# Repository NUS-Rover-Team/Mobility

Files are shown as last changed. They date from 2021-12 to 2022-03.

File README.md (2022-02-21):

# Mobility

The mobility system of the rover is comprised of a wheel sub-assembly, rocker-bogie suspension and a differential joint connecting the suspension to the chassis. 

## Rocker Bogie Suspension
This suspension was chosen to ensure the chassis remains parallel to the ground at all times. Furthermore, the system is designed such that the rover can traverse objects up to 30cm in height, without compromising the stability of the system. All components in the suspension are manufactured using Aluminium 6065, which was chosen for its light weight, tensile strength and manufacturability. 

## Wheels and Motors
The wheels on New Opportunity are made from durable, puncture-resistant rubber and are inflatable. This allows us to adjust the pressure within the wheels based on the terrain. 170KV brushless DC motors by Alien Power Systems were chosen since they provide high torque at a low RPM, have sufficient documentation and are reliable. The motors are controlled via Flipsky VESCs using PPM signals from the on-board ATmega328P-based microcontroller. 

## Suspension-Chassis Joint
The self-levelling mechanism is guided by the rotating differential bar attached to the chassis and rocker. 

## Control Scheme
The rover is steered using a 6-wheeled differential drive mechanism. The six wheels on the rover rotate at different velocities to achieve a desired rotation/movement. The control input comes from a joystick/autonomous command, which provides coordinates to the microcontroller, which in turn runs the motors at calculated velocities. The control scheme also uses a PID controller with a negative feedback loop to account for differences in velocities which may occur due to terrain/obstacles.

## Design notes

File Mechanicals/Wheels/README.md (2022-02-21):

# How to fix the wheels to the motor mounts and motors?

## Step 1: Grab one of the inflated wheels, place it like this:

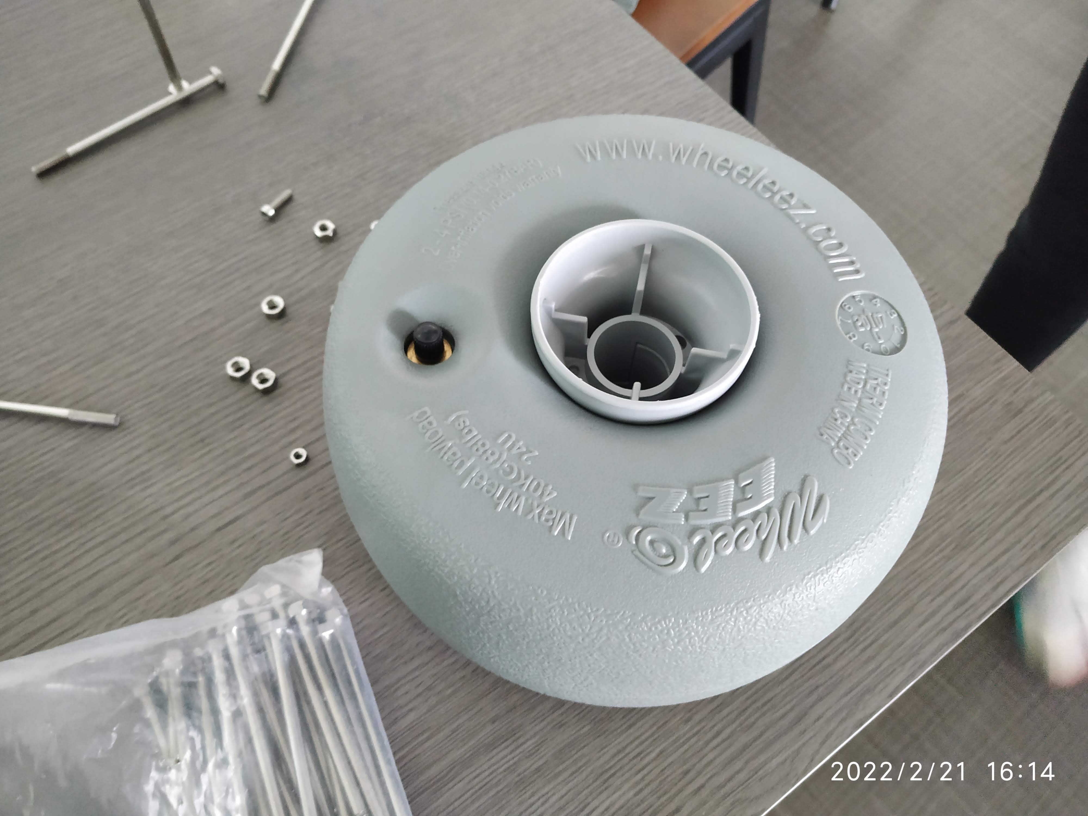
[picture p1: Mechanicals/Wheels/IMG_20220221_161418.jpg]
Step1


## Step 2: Add the plastic circular connector to the centre, make sure it aligns with the holes in the centre:

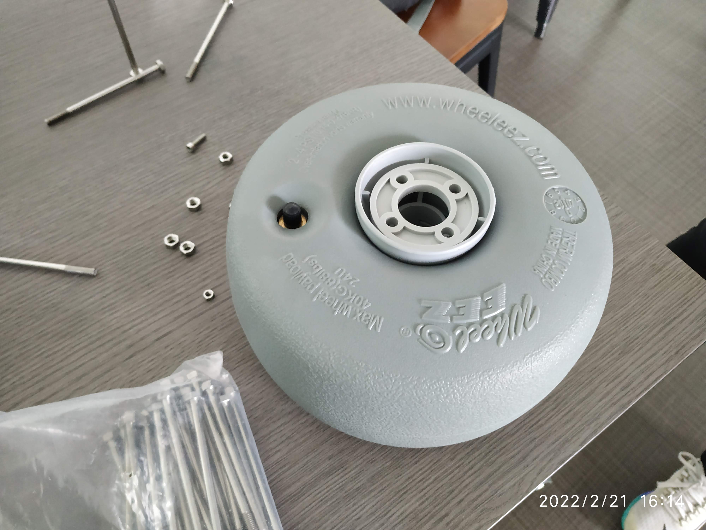
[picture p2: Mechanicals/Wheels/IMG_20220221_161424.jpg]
Step2


## Step 3: Flip it over and add the large screws in the 4 holes 

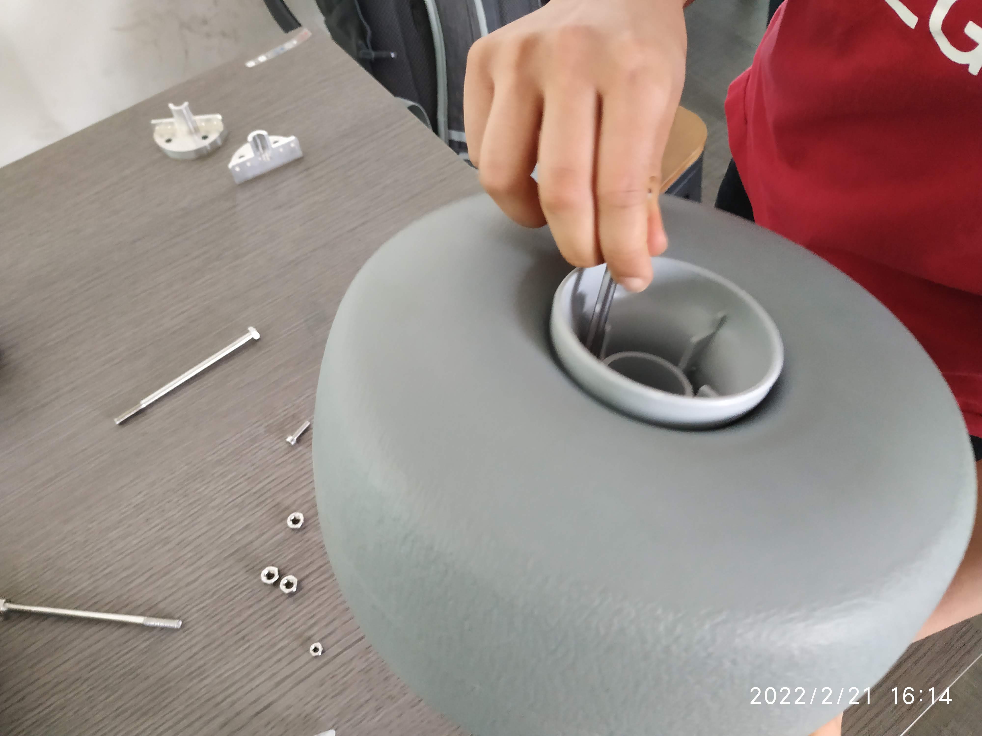
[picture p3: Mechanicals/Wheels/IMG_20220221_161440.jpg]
Step 3


## Step 4: It should look like this:

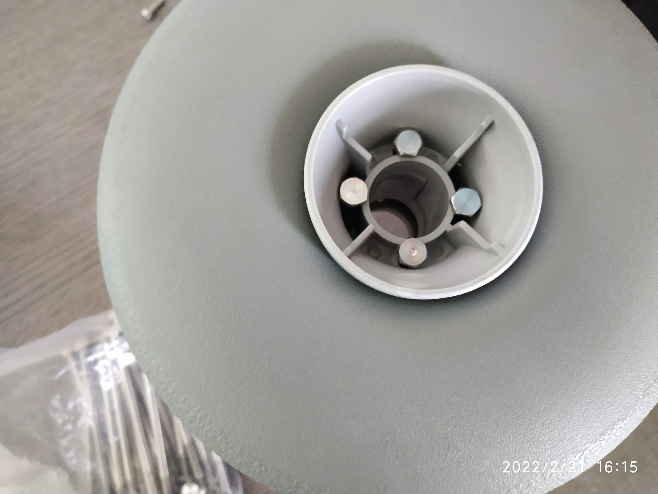
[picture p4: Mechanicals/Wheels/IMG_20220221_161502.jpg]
Step 4


## Step 5: Flip it over it will look something like this. You must hold on to the screws at this point or they'll fall out.

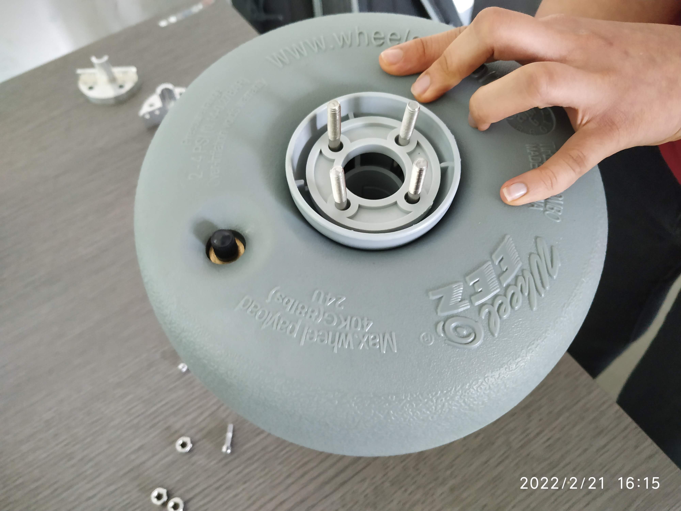
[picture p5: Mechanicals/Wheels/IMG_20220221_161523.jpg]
Step 5


## Step 6: Add the metal connector clamp to this. Most of them have a fixed pair they clamp well with in the lab. 

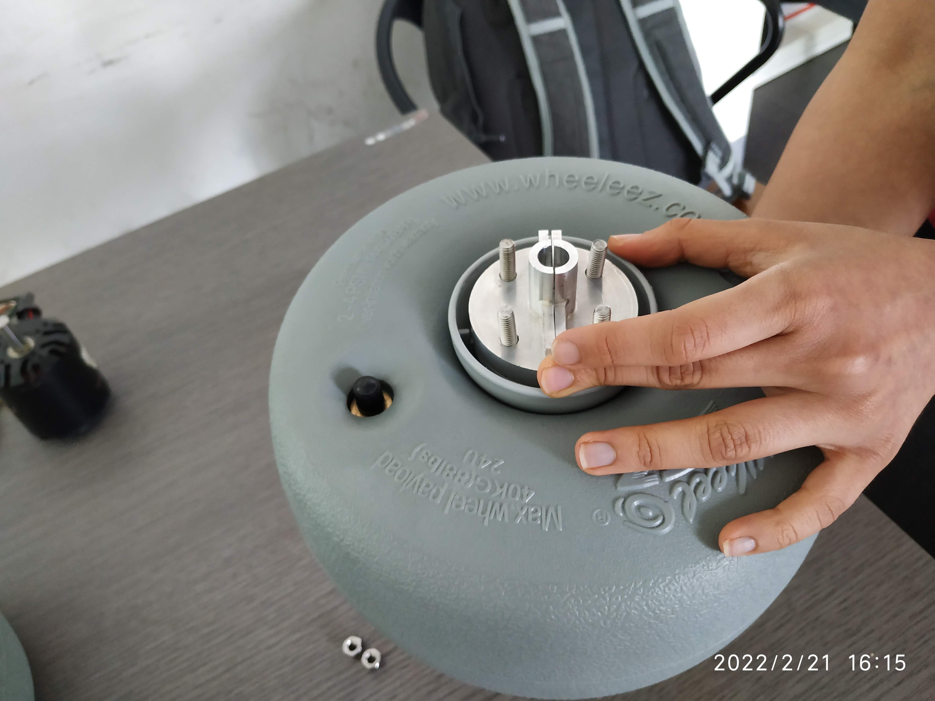
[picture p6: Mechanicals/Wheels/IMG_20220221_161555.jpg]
Step 6


## Step 7: Screw on the nuts for the large screws to hold everything in place:

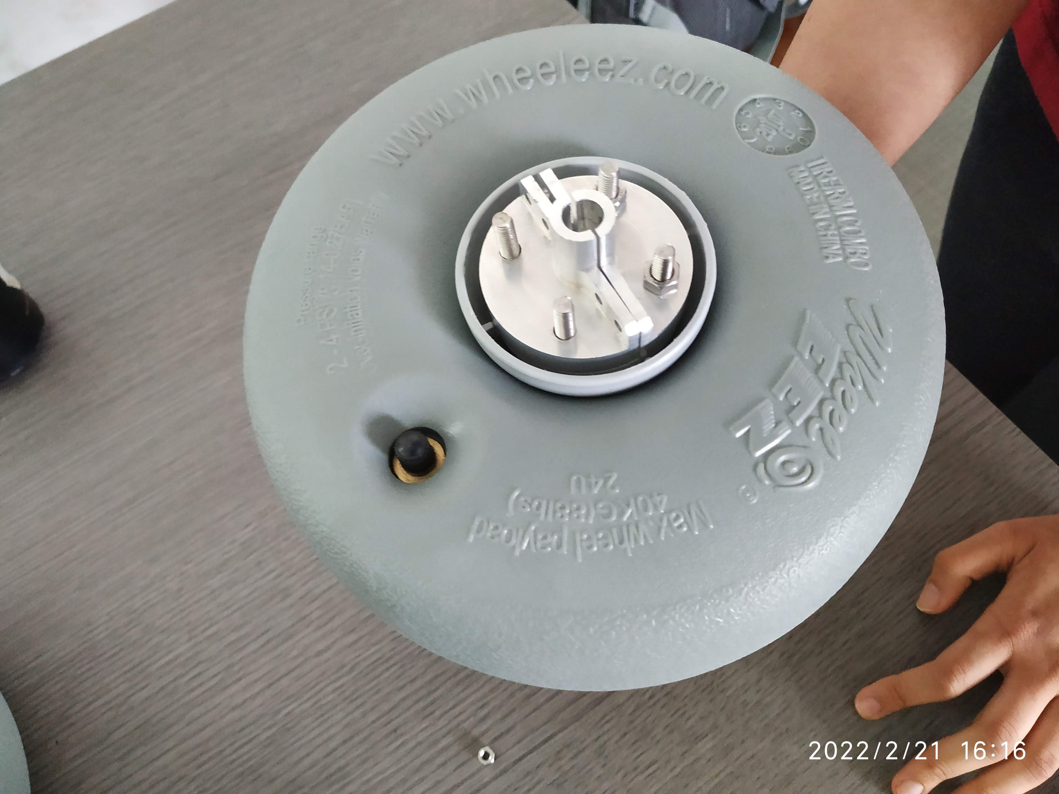
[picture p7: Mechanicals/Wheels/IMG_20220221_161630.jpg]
Step 7


## Step 8: Put the motor shaft in the connector

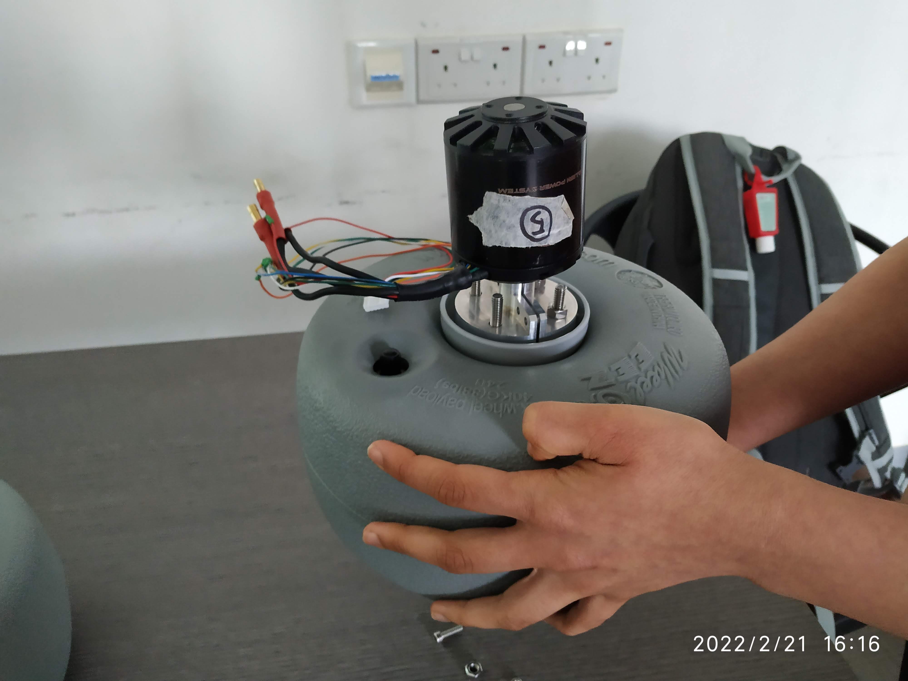
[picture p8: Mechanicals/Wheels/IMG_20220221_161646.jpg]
Step 8


## Step 9: Fasten the connector with M5 screws and nuts:

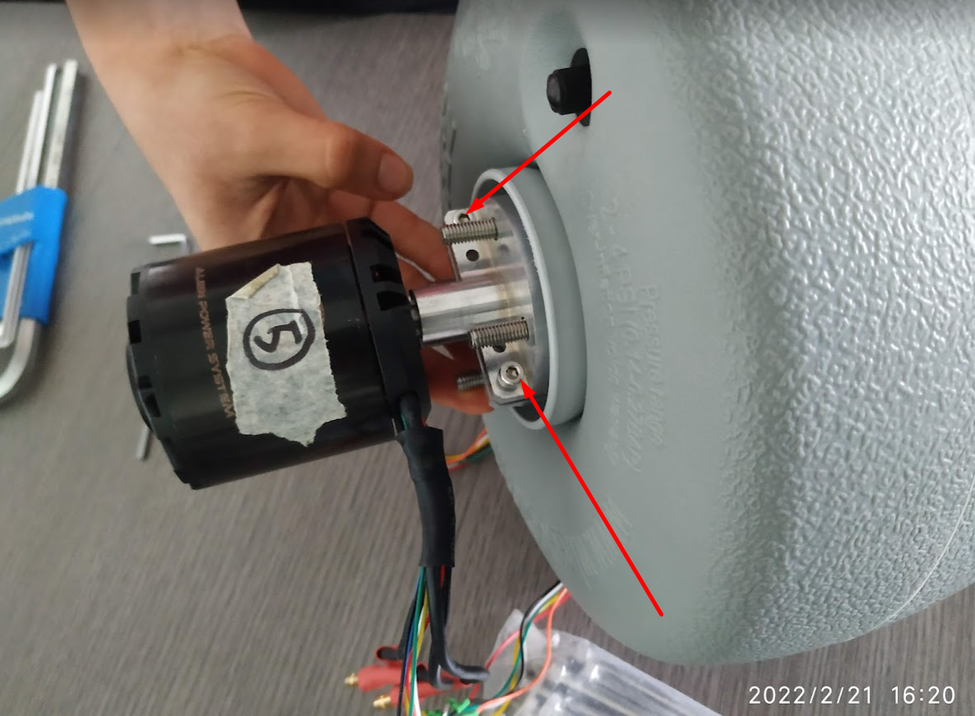
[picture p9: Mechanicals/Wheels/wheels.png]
Step 9


## Step 10: Slip the motor mount on and you're good to go!

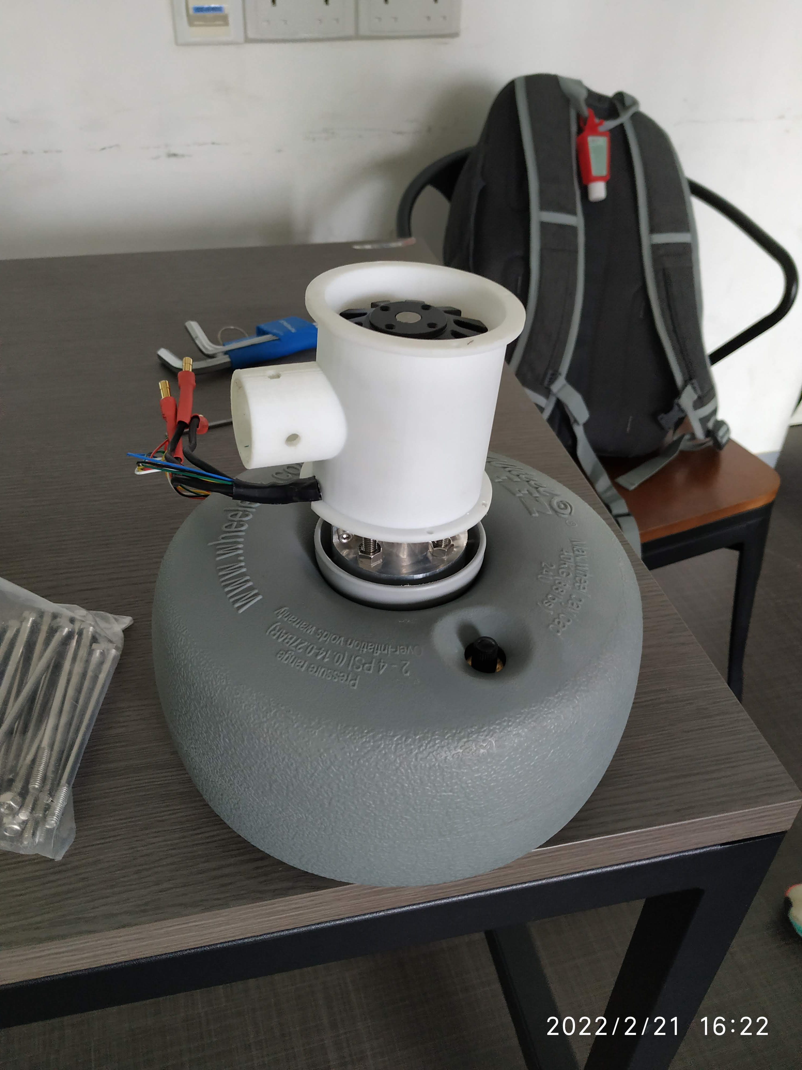
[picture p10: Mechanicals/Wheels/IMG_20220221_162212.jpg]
Step 10


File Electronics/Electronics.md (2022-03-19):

# Mobility Circuit

mobility-motor-circuit-diagram

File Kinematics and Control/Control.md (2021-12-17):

# Inv Kin for 6 Wheeled Differential Drive

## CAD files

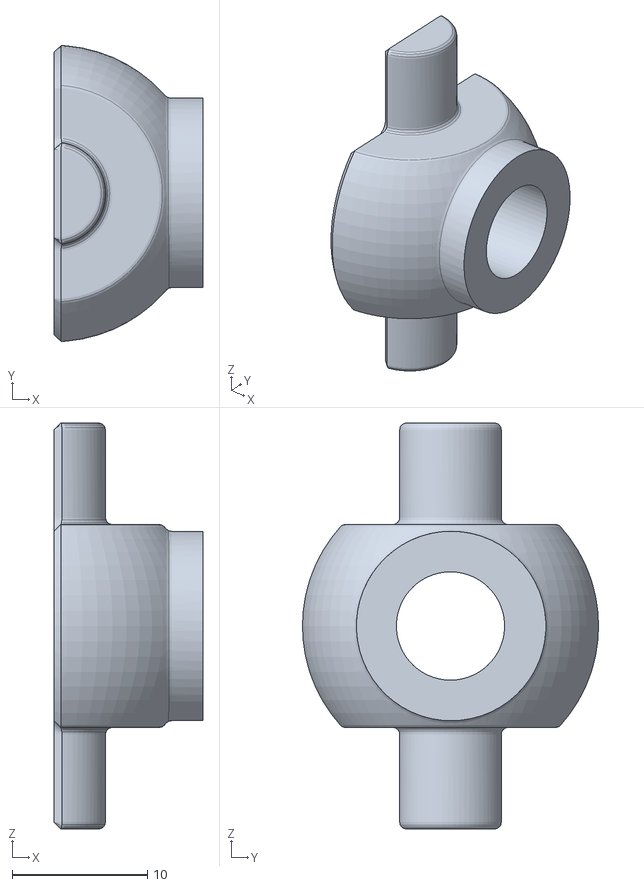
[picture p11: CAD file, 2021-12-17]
Mechanicals/New Differential Design (Sawppy)/Rod Support (QTY = 2).stl
11.0 x 21.9 x 30.0

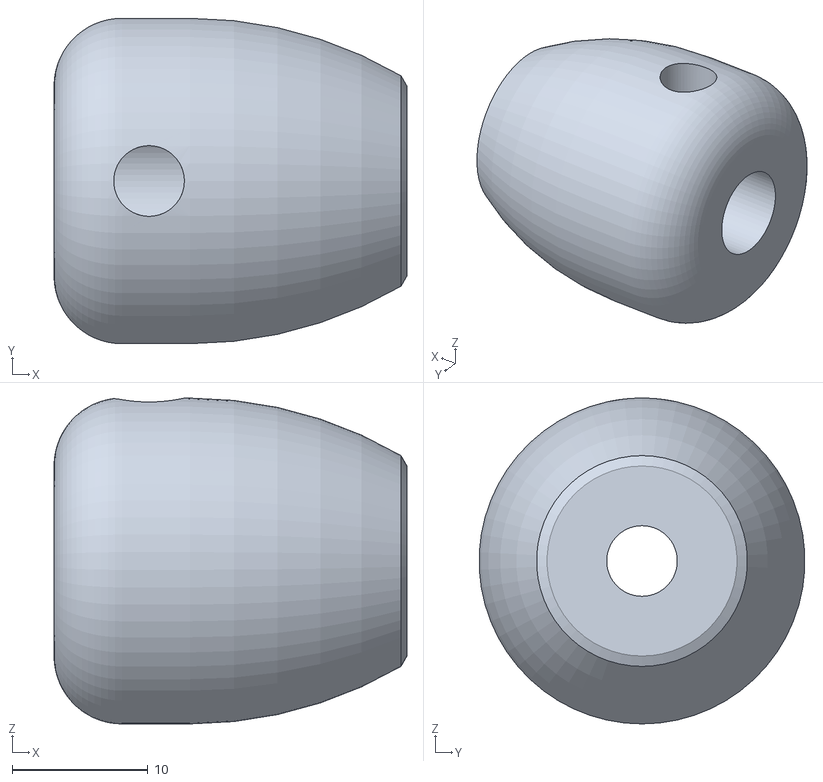
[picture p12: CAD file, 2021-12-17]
Mechanicals/New Differential Design (Sawppy)/DiffLink (QTY = 2).stl
26.0 x 24.0 x 24.0

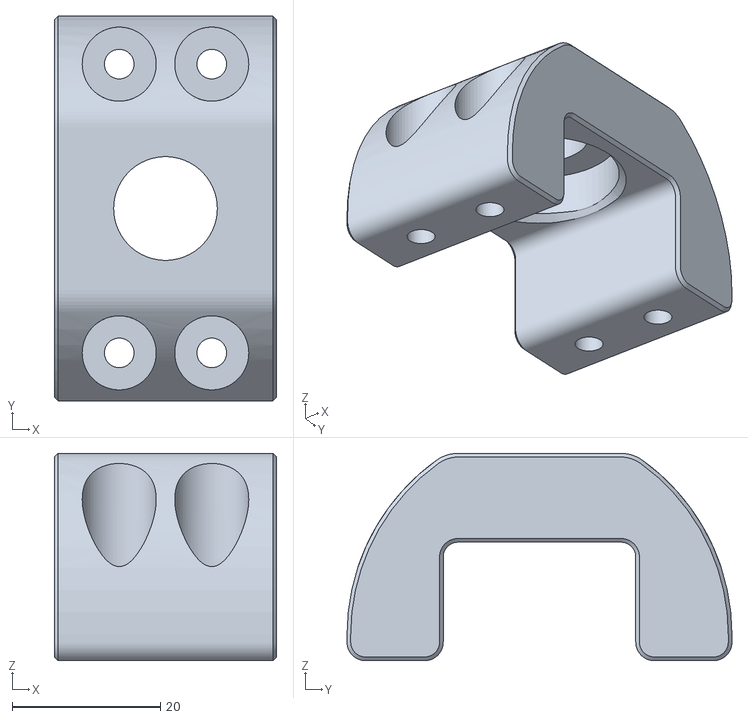
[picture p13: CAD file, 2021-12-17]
Mechanicals/New Differential Design (Sawppy)/DiffUpper (QTY = 1).stl
30.0 x 52.0 x 28.0

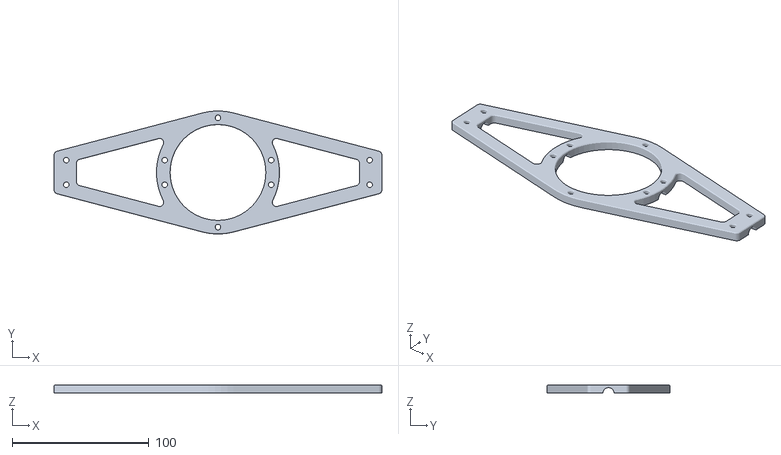
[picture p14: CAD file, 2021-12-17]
Mechanicals/New Differential Design (Sawppy)/DiffBrace (QTY = 2).stl
240.0 x 89.9 x 6.00

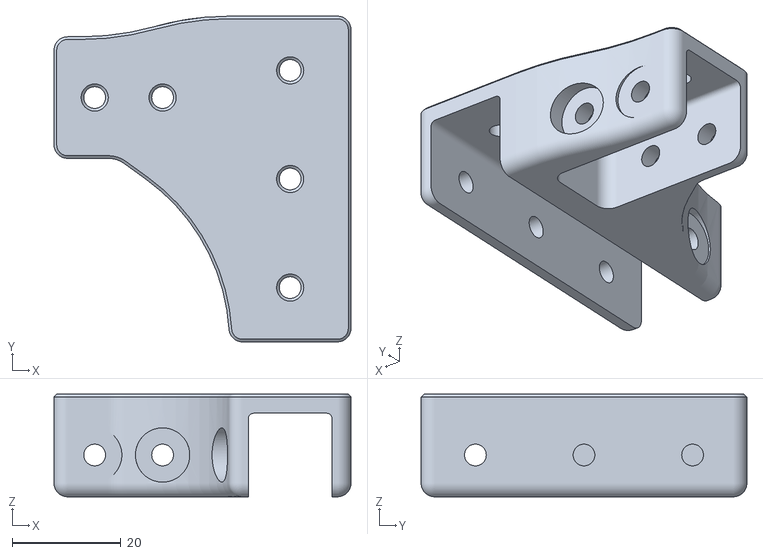
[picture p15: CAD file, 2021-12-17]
Mechanicals/New Differential Design (Sawppy)/DiffEnd (QTY = 2 MIRROR 1).stl
54.7 x 60.0 x 18.9

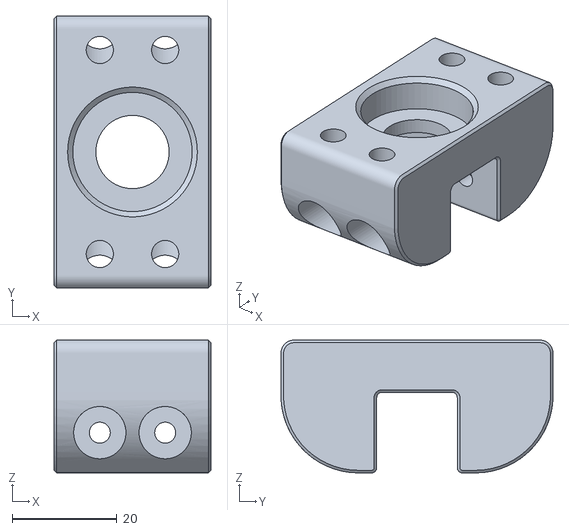
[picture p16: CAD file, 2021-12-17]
Mechanicals/New Differential Design (Sawppy)/DiffLower (QTY = 1).stl
30.0 x 52.0 x 25.4

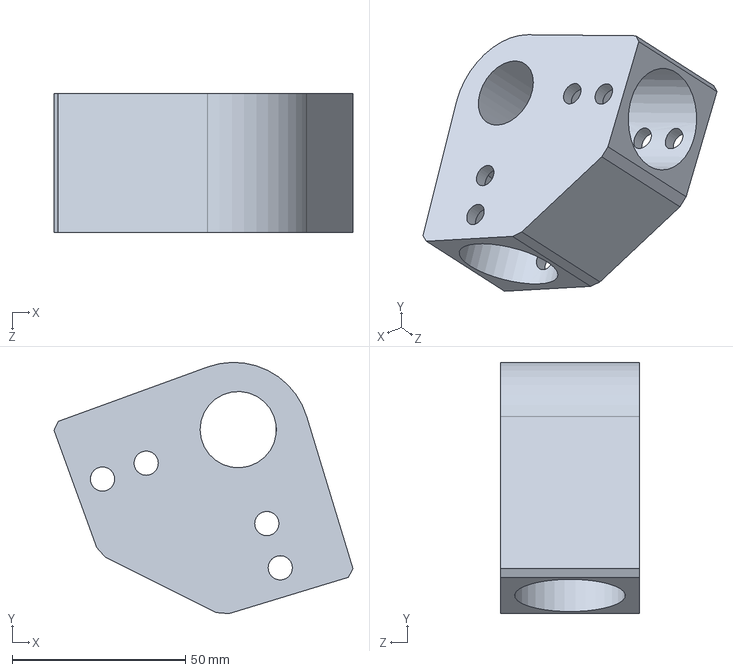
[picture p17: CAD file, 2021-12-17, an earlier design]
Mechanicals/Old Parts/Bogie/New Bogie Joint (QTY = 2).SLDPRT
86.2 x 72.5 x 40.0 mm

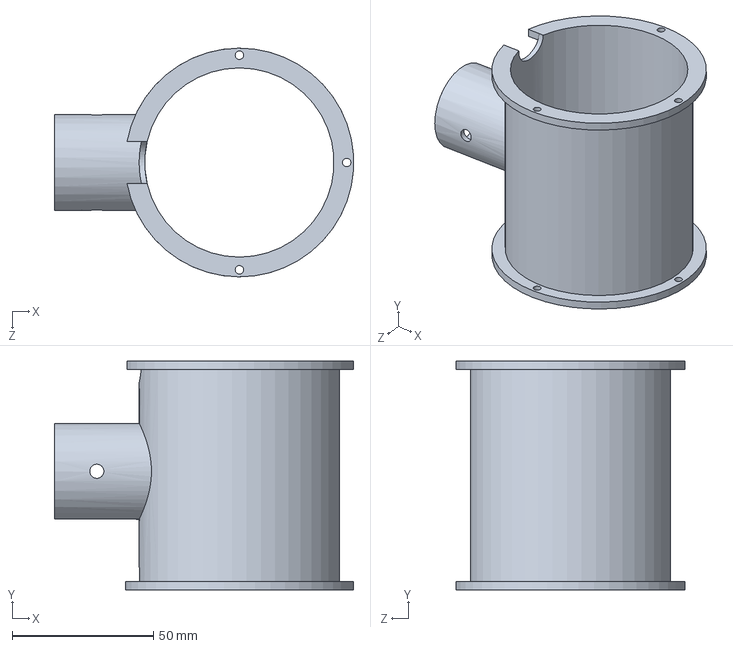
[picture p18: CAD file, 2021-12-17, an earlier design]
Mechanicals/Old Parts/Motor/Motor Housing New v1.1 (QTY = 6).SLDPRT
105.9 x 81.0 x 81.0 mm

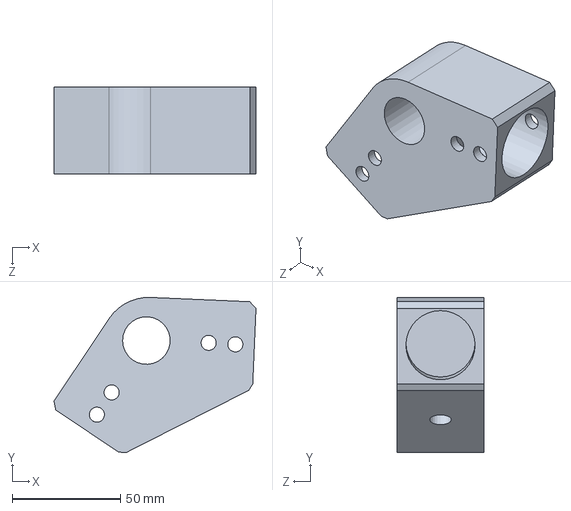
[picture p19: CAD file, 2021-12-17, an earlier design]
Mechanicals/Old Parts/Rocker/New Rocker Joint (QTY = 2).SLDPRT
93.4 x 71.7 x 40.0 mm

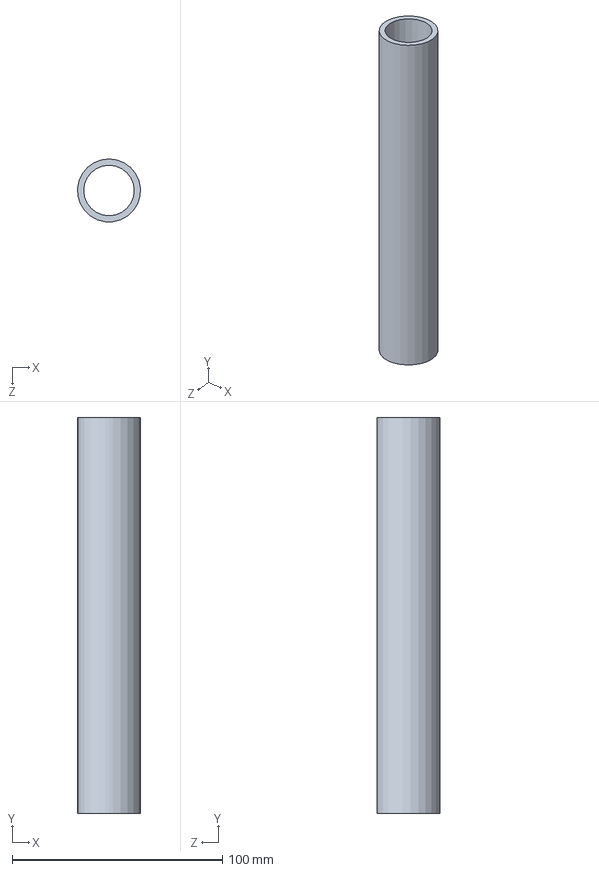
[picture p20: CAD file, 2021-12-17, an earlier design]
Mechanicals/Old Parts/Bogie/Bogie Rod (QTY = 4).SLDPRT
29.9 x 188.2 x 30.0 mm

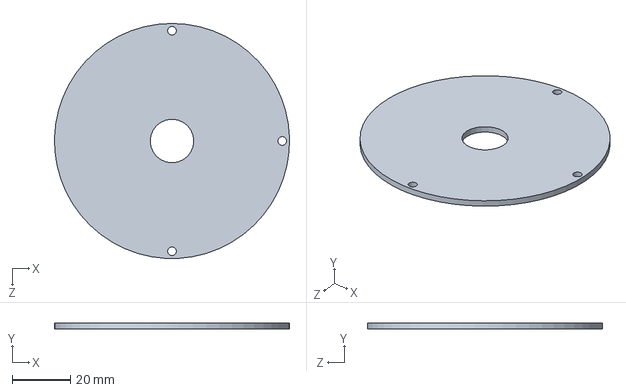
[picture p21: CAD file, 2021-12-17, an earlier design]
Mechanicals/Old Parts/Motor/Motor Housing Top Cover (QTY = 6).SLDPRT
81.0 x 2.00 x 81.0 mm

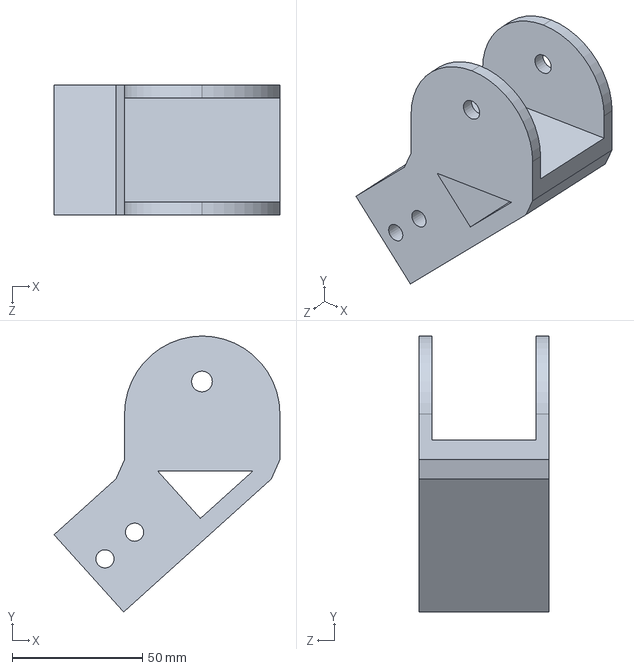
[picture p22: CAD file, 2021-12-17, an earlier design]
Mechanicals/Old Parts/Rocker/New Rocker Bracket (QTY = 2).SLDPRT
86.9 x 106.1 x 50.0 mm

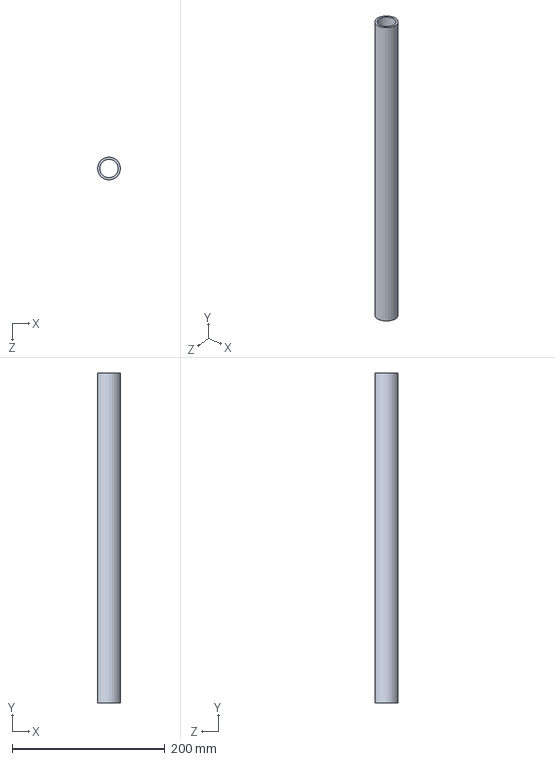
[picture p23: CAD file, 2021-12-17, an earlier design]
Mechanicals/Old Parts/Rocker/Rocker Rod Long (QTY = 2).SLDPRT
30.0 x 432.0 x 30.0 mm

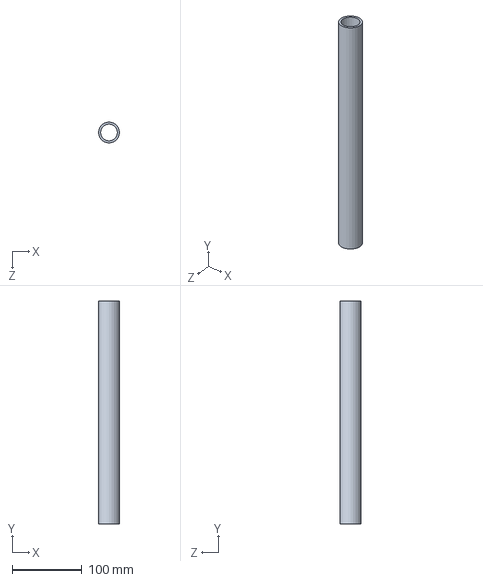
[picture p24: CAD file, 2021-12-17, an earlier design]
Mechanicals/Old Parts/Rocker/Rocker Rod short (QTY = 2).SLDPRT
30.0 x 320.0 x 30.0 mm

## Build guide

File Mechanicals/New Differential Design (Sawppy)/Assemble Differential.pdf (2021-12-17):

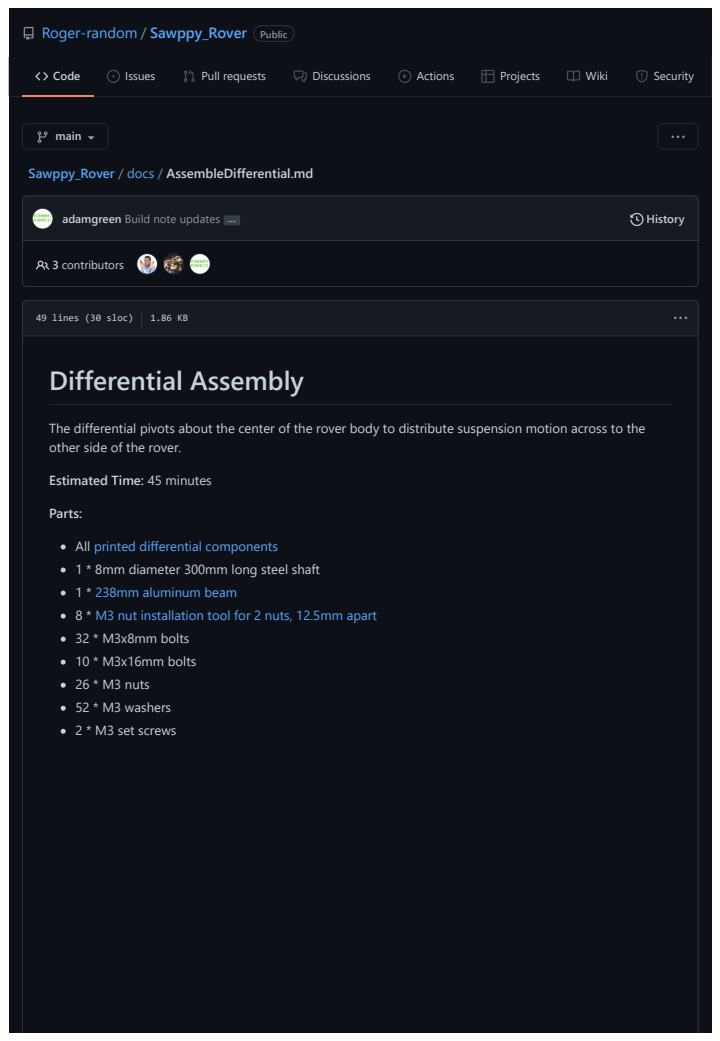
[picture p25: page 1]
Code; Issues; Pull requests; Discussions; Actions; Projects; Wiki; Security; adamgreen Build note updates …; History; 3 contributors; main; 49 lines (30 sloc); Differential Assembly

Roger-random (https://github.com/Roger-random) / Sawppy_Rover (https://github.com/Roger-random/Sawppy_Rover) Public

Sawppy_Rover (https://github.com/Roger-random/Sawppy_Rover) / docs (https://github.com/Roger-random/Sawppy_Rover/tree/main/docs) / AssembleDifferential.md

The differential pivots about the center of the rover body to distribute suspension motion across to the
other side of the rover.
Estimated Time: 45 minutes
Parts:
All printed differential components (https://github.com/Roger-random/Sawppy_Rover/blob/main/docs/Print%20Differential.md)
1 * 8mm diameter 300mm long steel shaft
1 * 238mm aluminum beam (https://github.com/Roger-random/Sawppy_Rover/blob/main/docs/Misumi%20HFS%203.md)
8 * M3 nut installation tool for 2 nuts, 12.5mm apart (https://github.com/Roger-random/Sawppy_Rover/blob/main/docs/Print%20M3%20Installation%20Tool.md)
32 * M3x8mm bolts
10 * M3x16mm bolts
26 * M3 nuts
52 * M3 washers
2 * M3 set screws

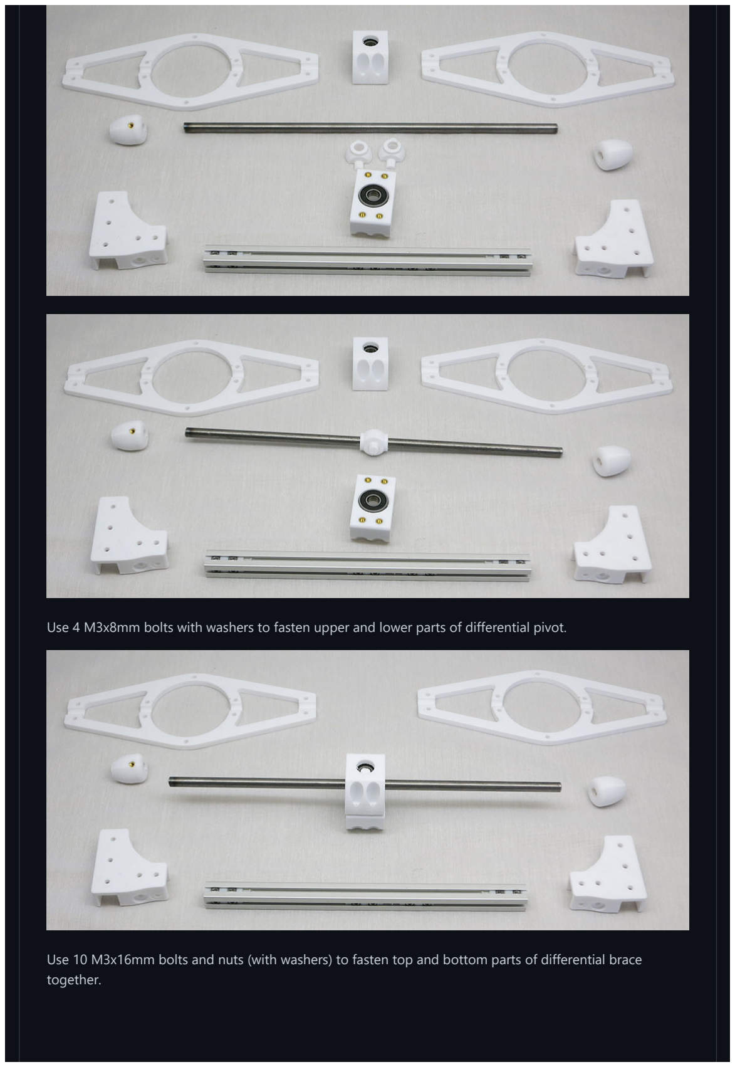
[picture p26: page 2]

Use 4 M3x8mm bolts with washers to fasten upper and lower parts of differential pivot.

Use 10 M3x16mm bolts and nuts (with washers) to fasten top and bottom parts of differential brace together.

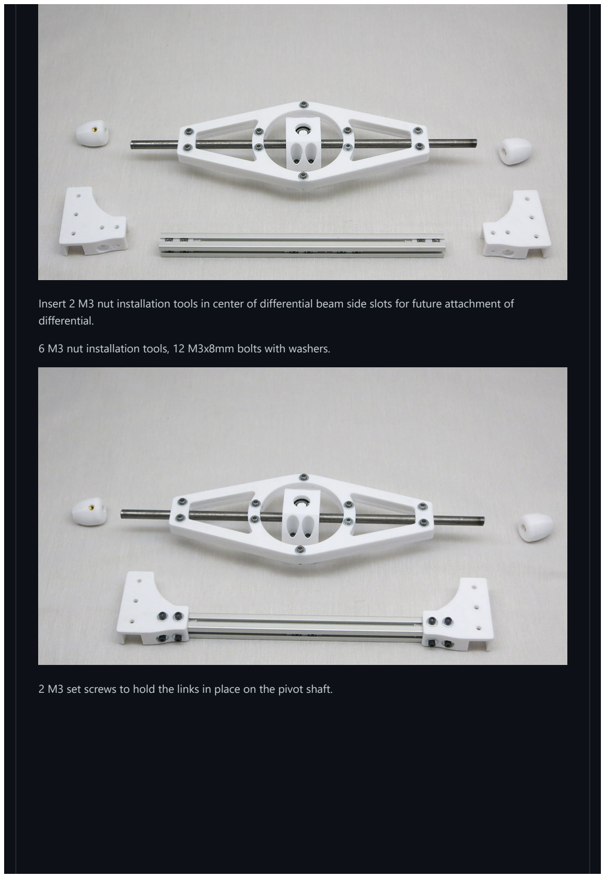
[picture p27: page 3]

Insert 2 M3 nut installation tools in center of differential beam side slots for future attachment of differential.

6 M3 nut installation tools, 12 M3x8mm bolts with washers.

2 M3 set screws to hold the links in place on the pivot shaft.

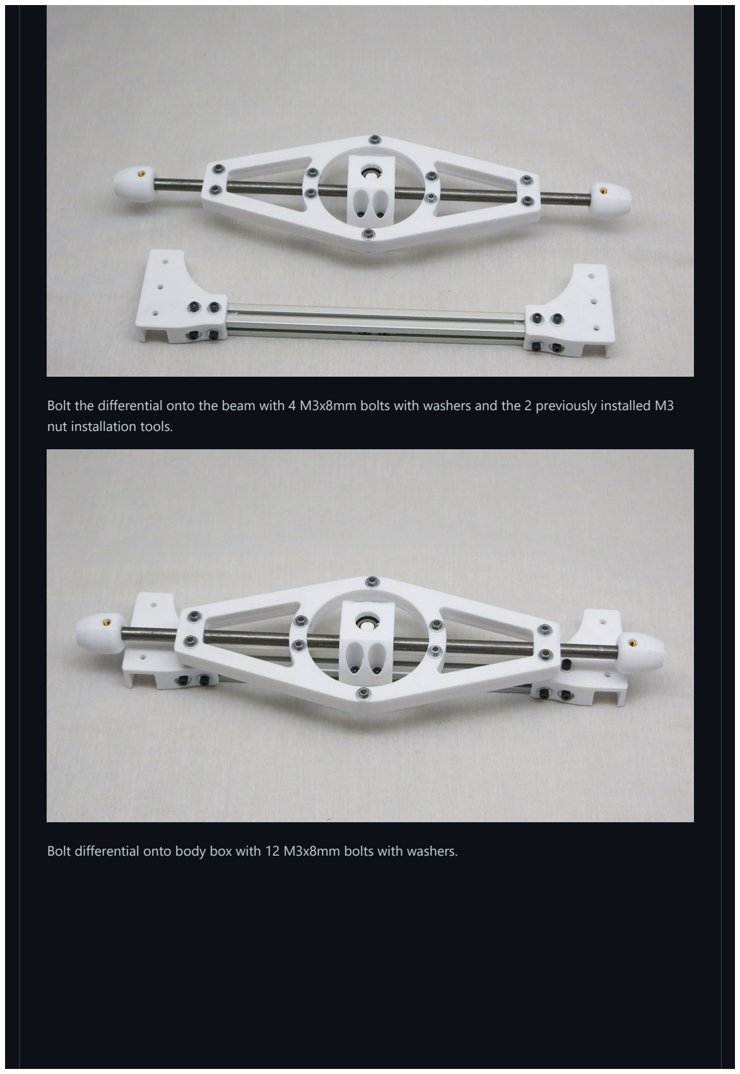
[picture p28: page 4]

Bolt the differential onto the beam with 4 M3x8mm bolts with washers and the 2 previously installed M3 nut installation tools.

Bolt differential onto body box with 12 M3x8mm bolts with washers.

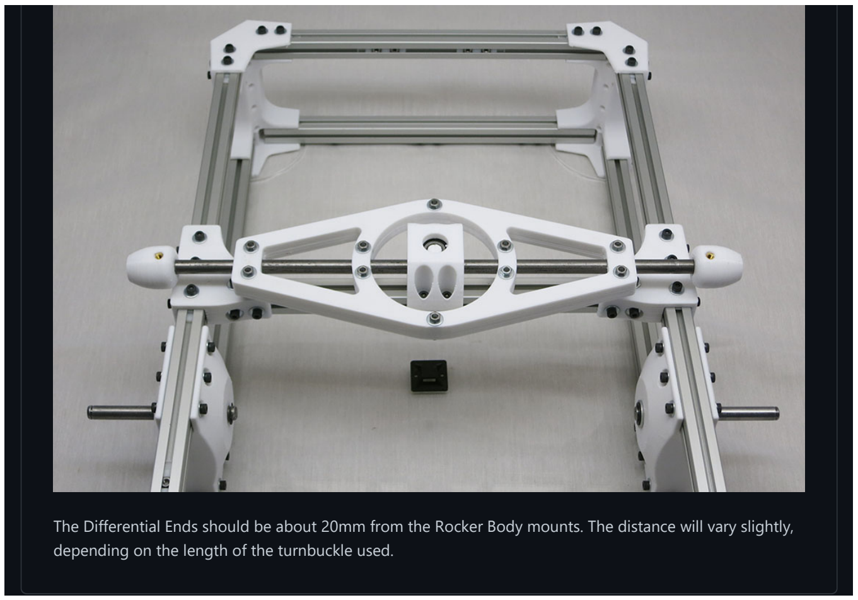
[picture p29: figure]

The Differential Ends should be about 20mm from the Rocker Body mounts. The distance will vary slightly, depending on the length of the turnbuckle used.

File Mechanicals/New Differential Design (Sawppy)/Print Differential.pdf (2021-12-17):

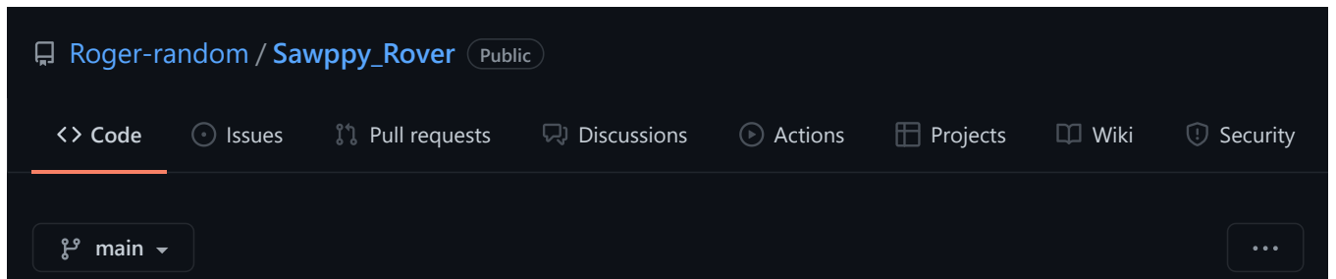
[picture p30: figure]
Roger-random / Sawppy_Rover Public; Code; Issues; Pull requests; Discussions; Actions; Projects; Wiki; Security; main

Sawppy_Rover (https://github.com/Roger-random/Sawppy_Rover) / docs (https://github.com/Roger-random/Sawppy_Rover/tree/main/docs) / Print Differential.md

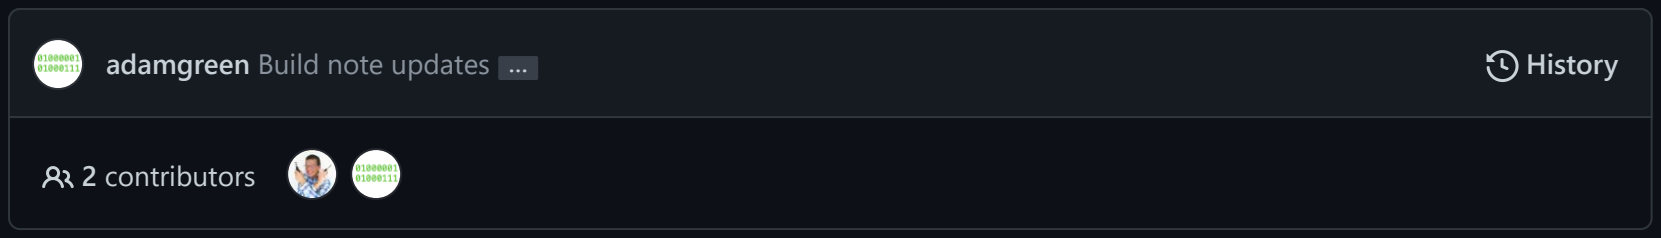
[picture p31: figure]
adamgreen Build note updates …; History; 2 contributors

43 lines (29 sloc) 2.07 KB

# Differential

The differential on Sawppy is different from the differential in an automotive drivetrain. Instead of distributing different forces across different drive wheels, this differential distributes suspension forces across the two sides. It is a key part of how the rocker-bogie suspension (https://en.wikipedia.org/wiki/Rocker-bogie) keeps all six wheels on the ground.

CAD source Differential (https://cad.onshape.com/documents/43678ef564a43281c83e1aef/w/392bbf8745395bc24367a35c/e/ded3b96eec03ac1553f6b0a8) with brackets to mount to body in Body Box Mounts (https://cad.onshape.com/documents/43678ef564a43281c83e1aef/w/392bbf8745395bc24367a35c/e/4b42dffa042b70b94b3d0d85)

3D Printing STL Files:

DiffBrace.stl (https://github.com/Roger-random/Sawppy_Rover/blob/main/STL/DiffBrace.stl) * 2
DiffEnd.stl (https://github.com/Roger-random/Sawppy_Rover/blob/main/STL/DiffEnd.stl) * 2 (Mirror one of them) DiffLink.stl (https://github.com/Roger-random/Sawppy_Rover/blob/main/STL/DiffLink.stl) * 2
DiffLower.stl (https://github.com/Roger-random/Sawppy_Rover/blob/main/STL/DiffLower.stl) * 1
DiffUpper.stl (https://github.com/Roger-random/Sawppy_Rover/blob/main/STL/DiffUpper.stl) * 1
Rod Support.stl (https://github.com/Roger-random/Sawppy_Rover/blob/main/STL/Rod%20Support.stl) * 2

3D Printing Notes:

The differential brace (https://github.com/Roger-random/Sawppy_Rover/blob/main/STL/DiffBrace.stl) is a large part that needs to be rotated 45 degrees in order to fit on a 200mm x 200mm print bed.
Aside from the differential brace, everything else can be printed together.

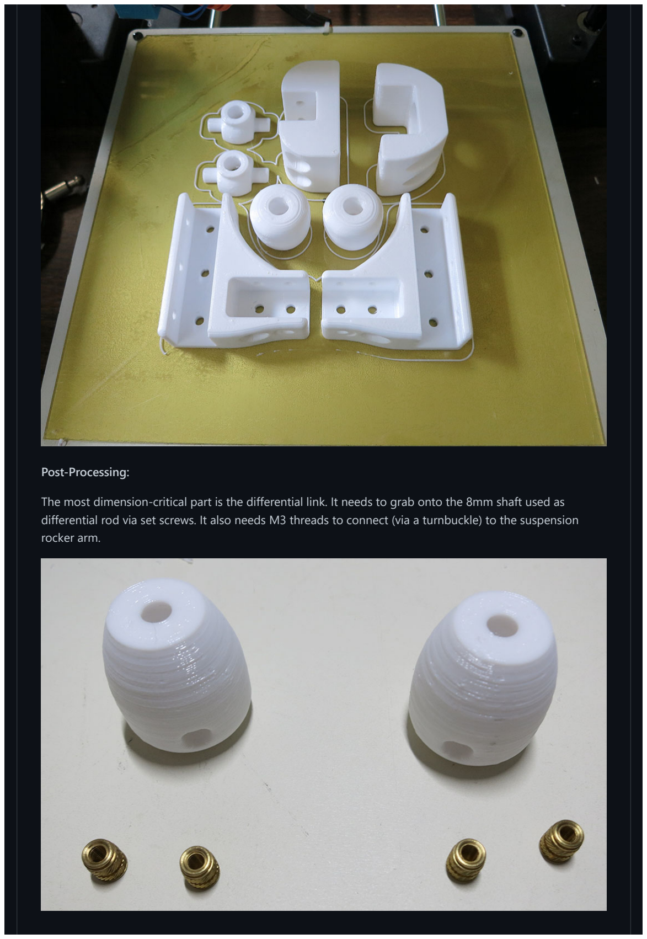
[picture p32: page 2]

Post-Processing:

The most dimension-critical part is the differential link. It needs to grab onto the 8mm shaft used as differential rod via set screws. It also needs M3 threads to connect (via a turnbuckle) to the suspension rocker arm.

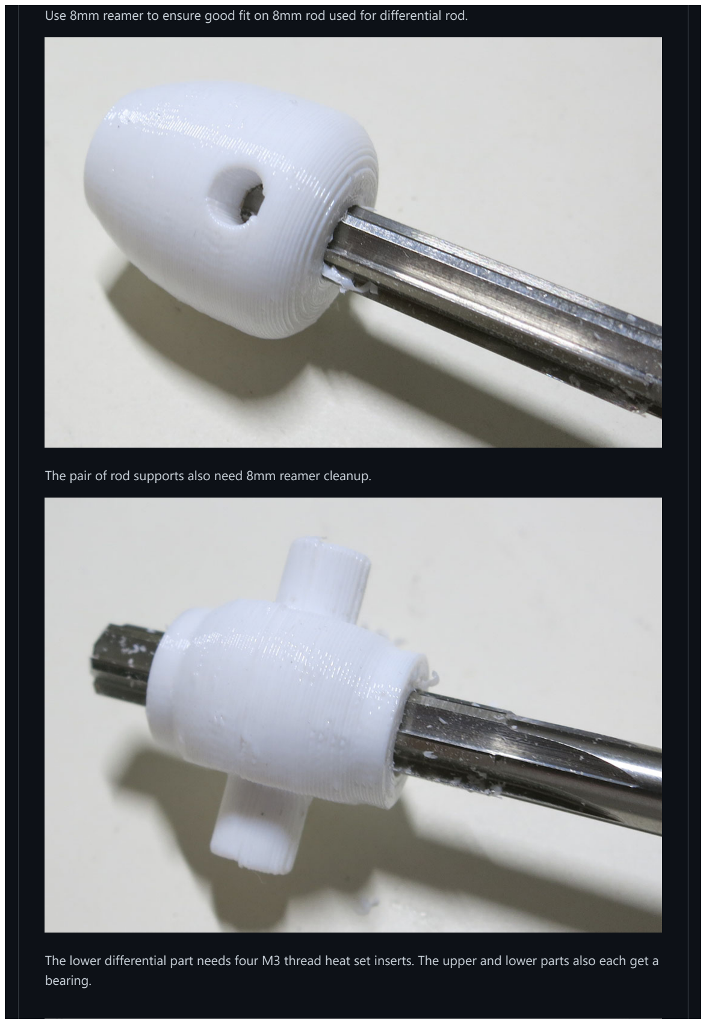
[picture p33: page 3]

Use 8mm reamer to ensure good fit on 8mm rod used for differential rod.

The pair of rod supports also need 8mm reamer cleanup.

The lower differential part needs four M3 thread heat set inserts. The upper and lower parts also each get a bearing.

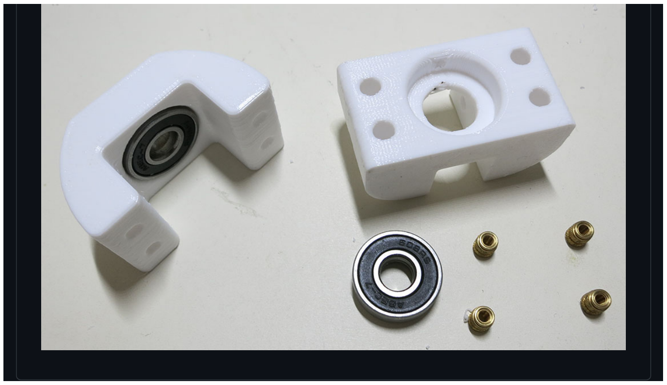
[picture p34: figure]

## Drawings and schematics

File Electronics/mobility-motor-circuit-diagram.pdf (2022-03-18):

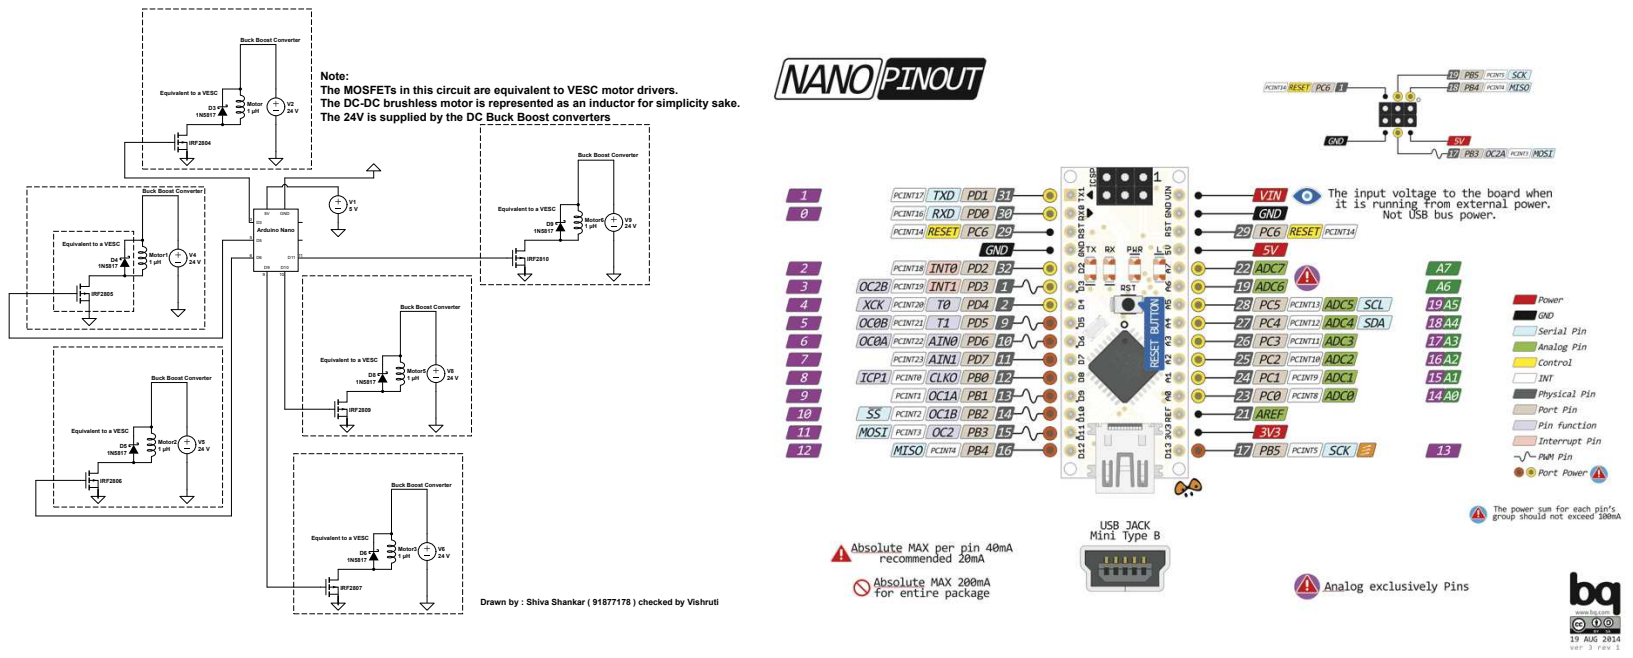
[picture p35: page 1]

Note:
The MOSFETs in this circuit are equivalent to VESC motor drivers.
The DC-DC brushless motor is represented as an inductor for simplicity sake.
The 24V is supplied by the DC Buck Boost converters

Drawn by : Shiva Shankar ( 91877178 ) checked by Vishruti

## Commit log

2021-12-17 Add parts that might need to be redesigned
    [Bogie Rod (QTY = 4).SLDPRT, Motor Housing New v1.1 (QTY = 6).SLDPRT, Motor Housing Top Cover (QTY = 6).SLDPRT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]
2021-12-17 Add sawppy rover differential bar files
    [DiffBrace (QTY = 2).stl, DiffEnd (QTY = 2 MIRROR 1).stl, DiffLink (QTY = 2).stl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]
2022-03-18 Added Mobility Circuit Diagram
    - Final Revision of Mobility circuit
2022-03-19 Uploaded Mobility Circuit Diagram
